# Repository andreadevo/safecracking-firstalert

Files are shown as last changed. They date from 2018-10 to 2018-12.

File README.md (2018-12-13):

# safecracking-firstalert
Building and designing a robot to open a safe with an unknown combination.

Link to photo and video documenation: http://bit.ly/first-alert-documentation

Try times:
100 possible numbers for 3 disks:
100x100x100 = 1,000,000 combinations
Each number can be +/- 1
Not likely or possible to duplicate numbers between disks
33x32x32 = 34,848
13 seconds per test means 5.25 days (without set testing)

We know the disks were only moved around and the first and last disk cannot move.
This means that the first number of the combination has to be 97 and the last must be 0.
1x33x32 = 1,056 combinations
13 seconds per test means 3.81 hours (without set testing)

After looking at the disks inside the safe we saw that they were split into 17 equal, numbered sections where interference points were placed.
The disk closest to the door had one interference point at 9 facing inward towards the safe.
The second two disks were identical and had interference points at 7 on one side and 3 on the other.
Then the disk farthest from the door had an interference point at 10 facing outward towards the door.
We know that the two middle disks are identical and only have two orientations.
We also know that the first and last disks cannot move or be changed.
So we have four possible orientations of the disks and their interference points.
(9)(7/3)(7/3)(10),
(9)(7/3)(3/7)(10),
(9)(3/7)(7/3)(10),
(9)(3/7)(3/7)(10).

This means there are only four possible combinations, one of which is the old one, so in reality, three possible combinations.
(97,32,44,0),
(97,32,??,0),
(97,??,44,0),
(97,??,??,0).

We can guess that most likely both middle disks were flipped to create more mystery
If we find which orientation the old disks were we can model the new orientation and find a range where the missing numbers could be so that we can make our blunt force test WAY faster than 4 hours. Ideally we should find a range of 10 or 15 which would be 3 to 5 set tests.
1x3x3 = 2 minutes
1x5x5 = 5.5 minutes

Even if we settled for finding a range of 48 values (figuring out right/left numbers of dial or top/bottom numbers of dial) it would be 16 tests.
1x16x16 = 55 minutes

Even though we ended up testing only 4 possible combinations, the blunt force test time for the right one (97, 7, 67) would be
1x2x50 = 25 minutes (testing up until getting the correct second number) + 1x1x34 = 8.5 minutes (last test with correct second number until reaching the correct 3rd number).
Being a total of 33.5 minutes to find this particular combination with our tests checking every other number to make up for any slop in the system.

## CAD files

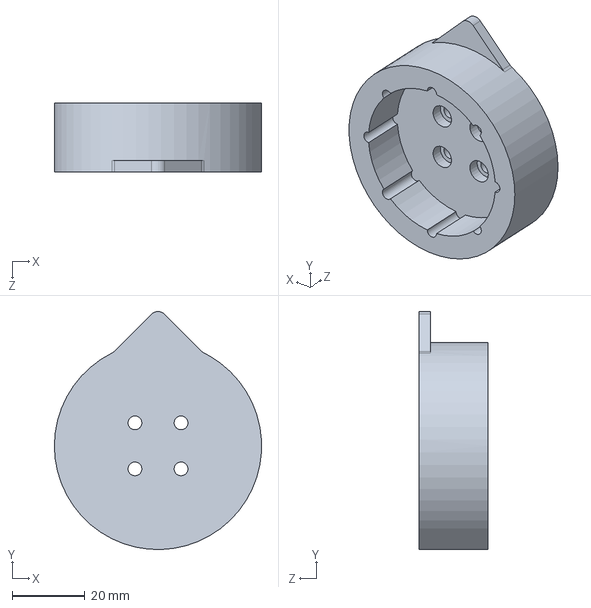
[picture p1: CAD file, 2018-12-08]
Parts/DIALCOUPLER.SLDPRT
57.1 x 65.6 x 19.1 mm

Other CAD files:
Parts/DIALCOUPLER.STL

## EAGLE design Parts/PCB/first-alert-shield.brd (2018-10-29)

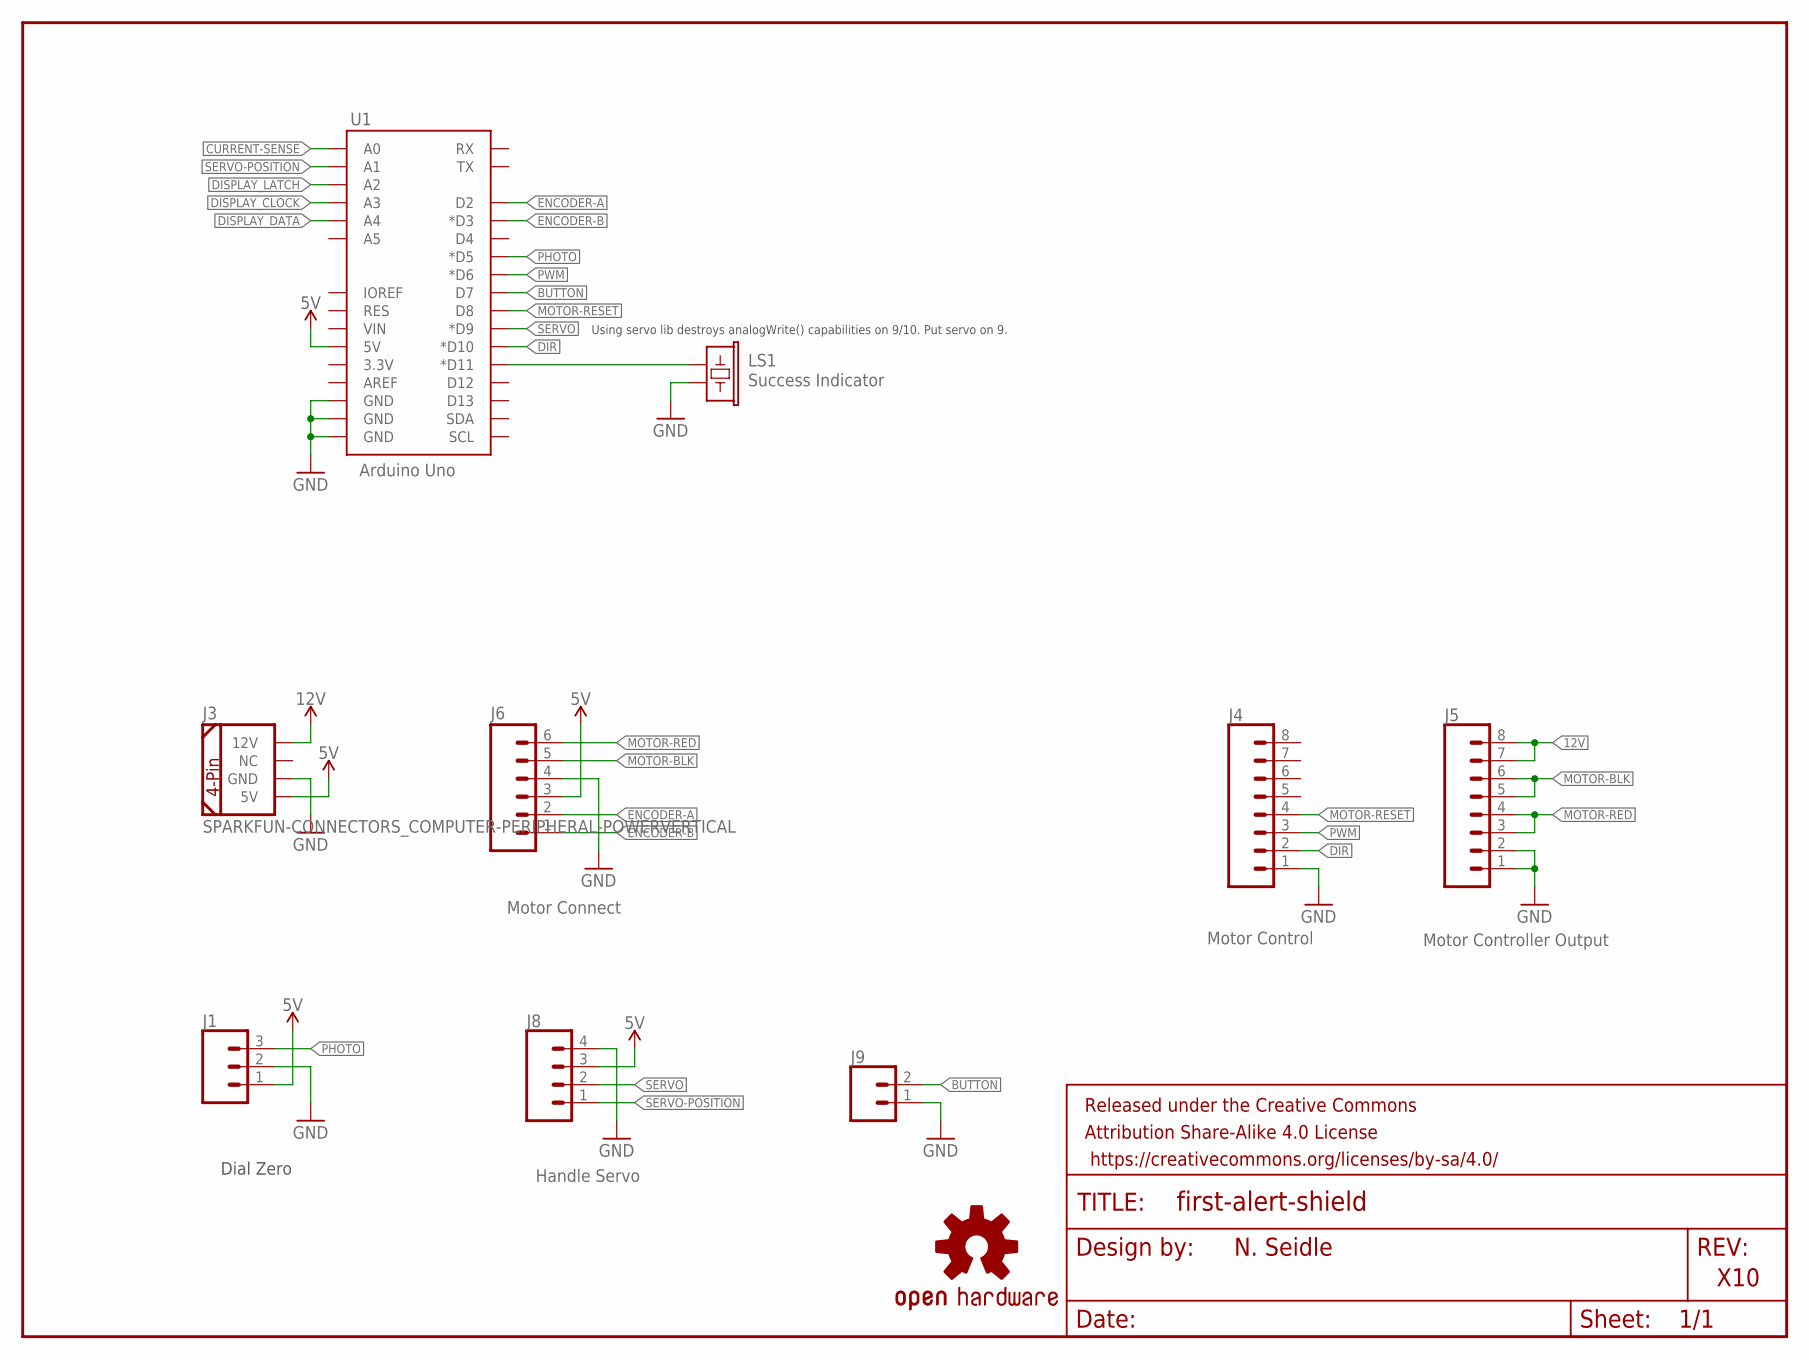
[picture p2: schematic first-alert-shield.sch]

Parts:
FRAME1: FRAME-LETTER; CREATIVE_COMMONS
J1: CONN_03JST-PTH-VERT; JST-3-PTH-VERT
J3: SPARKFUN-CONNECTORS_COMPUTER-PERIPHERAL-POWERVERT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; SPARKFUN-CONNECTORS_COMPUTER-PERIPHERAL-POWER
J4: Motor Control; 1X08
J5: Motor Controller Output; 1X08
J6: Motor Connect; 1X06@1
J8: Handle Servo; 1X04
J9: CONN_02JST-PTH-VERT; JST-2-PTH-VERT
LOGO2: OSHW-LOGOS; OSHW-LOGO-S
LS1: Success Indicator; BUZZER-12MM
U1: Arduino Uno; UNO_R3_SHIELD_NOLABELS

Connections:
5V: J1.1, J3.5V, J6.3, J8.3, U1.5V
12V: J3.12V, J5.7, J5.8
BUTTON: J9.2, U1.D7
BUZZ: LS1.+ (1), U1.D11 (*D11)
CURRENT-SENSE: U1.A0
DIR: J4.2, U1.D10 (*D10)
DISPLAY_CLOCK: U1.A3
DISPLAY_DATA: U1.A4
DISPLAY_LATCH: U1.A2
ENCODER-A: J6.2, U1.D2
ENCODER-B: J6.1, U1.D3 (*D3)
GND: J1.2, J3.GND, J4.1, J5.1, J5.2, J6.4, J8.4, J9.1, LS1.- (2), U1.GND@0 (GND), U1.GND@1 (GND), U1.GND@2 (GND)
MOTOR-BLK: J5.5, J5.6, J6.5
MOTOR-RED: J5.3, J5.4, J6.6
MOTOR-RESET: J4.4, U1.D8
PHOTO: J1.3, U1.D5 (*D5)
PWM: J4.3, U1.D6 (*D6)
SERVO: J8.2, U1.D9 (*D9)
SERVO-POSITION: J8.1, U1.A1

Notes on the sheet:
N. Seidle
X10
Using servo lib destroys analogWrite() capabilities on 9/10. Put servo on 9.
Dial Zero

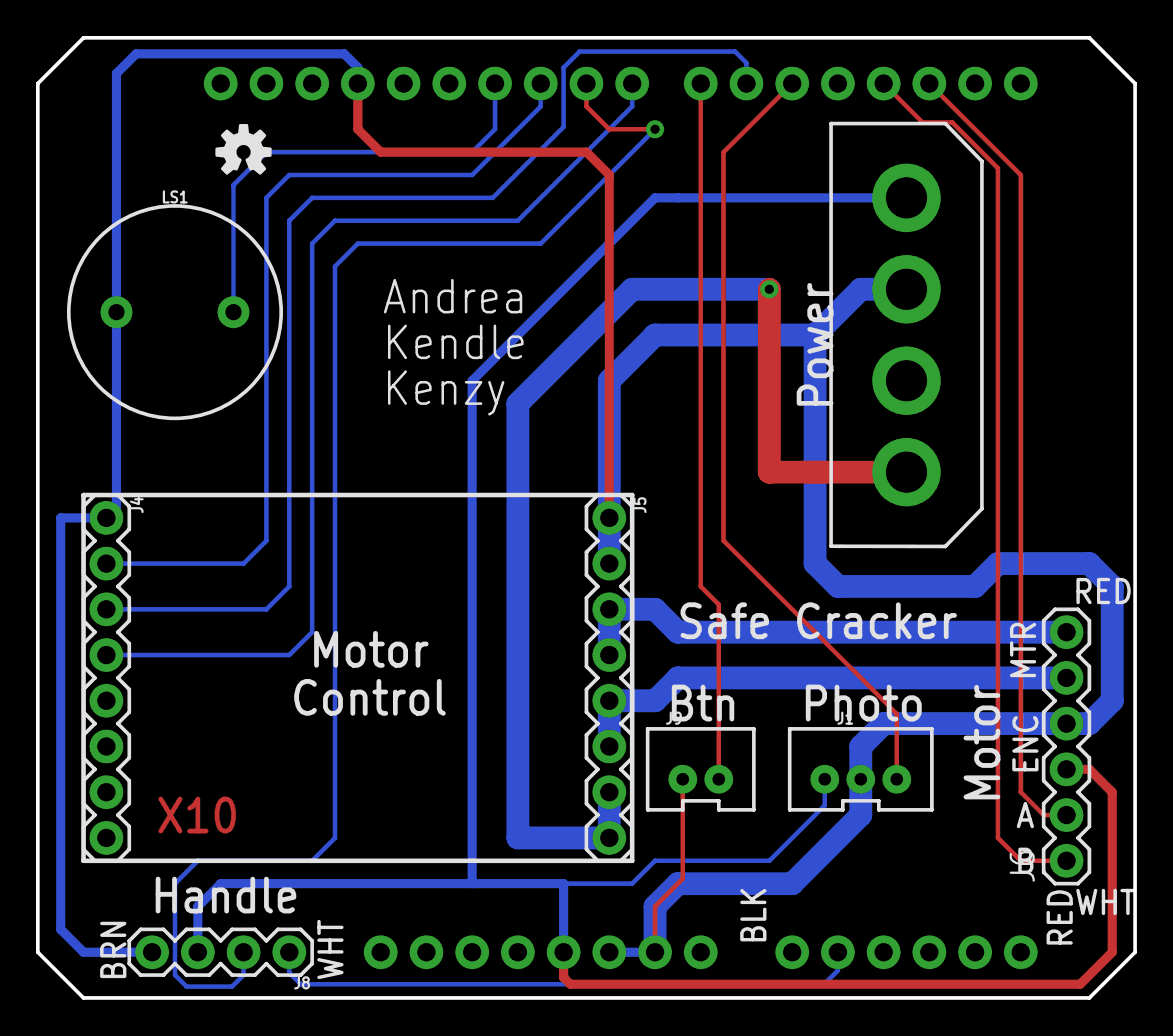
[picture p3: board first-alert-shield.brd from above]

Board: 2 copper layers, 61.0 x 53.3 mm, 11 parts (0 on the bottom side), 15 nets.

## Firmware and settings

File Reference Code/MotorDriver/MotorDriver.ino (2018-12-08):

/*
   Andrea DeVore
   Kenzy O'Neil
   Kendle
   Safecracking Class Fall 2018
   License: Open Source
*/

const int encoder0PinA = 2;
const int encoder0PinB = 3;
volatile unsigned int encoder0Pos = 0;

const int dirPin = 5;         // outputs the direction to dir pin on motor controller
const int pwmPin = 6;         // outputs high/low to PWM pin on motor controller, controls if motor is on/off
const int switchPin = 4;      // input from the switch, on/pff
const int photoGatePin = 7;   // input pin from photogate

int switchState;              // current state of the switch
int photoState;               // current state of the photogate

bool stateAChange = false;    // check if change has happened on A
bool stateBChange = false;    // check if change has happened on B

void setup() {
  // SETUP FOR ENCODER
  pinMode(encoder0PinA, INPUT_PULLUP);
  pinMode(encoder0PinB, INPUT_PULLUP);

  // encoder pin on interrupt 0 (pin 2)
  attachInterrupt(0, doEncoderA, CHANGE);
  // encoder pin on interrupt 1 (pin 3)
  attachInterrupt(1, doEncoderB, CHANGE);

  // SETUP FOR CONTROLS
  pinMode(dirPin, OUTPUT);
  pinMode(pwmPin, OUTPUT);
  pinMode(switchPin, INPUT);

  //LAUNCH MENU
  Serial.println("d)Dial position");
  Serial.println("h)Go home");

  Serial.begin(9600);
}

void loop() {
  //USER INPUT
  byte incoming;
  if (Serial.available()) {
    incoming = Serial.read();
    Serial.print("You pressed: ");
    Serial.write(incoming);
    Serial.println();

    // ROTATE DIAL TO USER INPUT
    if (incoming == 'd') {
      Serial.print("Enter dial position: ");
      while (!Serial.available());
      int dialPosition = Serial.parseInt();

      Serial.print("You told me to go to ");
      Serial.println(dialPosition);
      rotateDial(dialPosition);
    }
  }

  // LOOKS AT PHOTOGATE
  photoState = digitalRead(photoGatePin);
  if (photoState == HIGH) {
    // unbroken, motor on
    digitalWrite(pwmPin, HIGH);
  }
  else {
    // broken, motor off
    digitalWrite(pwmPin, LOW);
  }

  // LOOKS AT SWITCH
  switchState = digitalRead(switchPin);
  if (switchState == HIGH) {
    // switch on, CW
    digitalWrite(dirPin, HIGH);
  }
  else {
    // switch off, CCW
    digitalWrite(dirPin, LOW);
  }

  // CHECK IF ENCODER HAS MOVED
  if (stateAChange) {
    Serial.print ("A ");
    Serial.println (encoder0Pos, DEC);
    stateAChange = false;
  }
  if (stateBChange) {
    Serial.print ("B ");
    Serial.println (encoder0Pos, DEC);
    stateBChange = false;
  }
}

// ENCODER CODE
// encoder code from: playground.arduino.cc/Main/RotaryEncoders
void doEncoderA() {
  stateAChange = true;
  // look for a low-to-high on channel A
  if (digitalRead(encoder0PinA) == HIGH) {

    // check channel B to see which way encoder is turning
    if (digitalRead(encoder0PinB) == LOW) {
      encoder0Pos = encoder0Pos + 1;         // CW
    }
    else {
      encoder0Pos = encoder0Pos - 1;         // CCW
    }
  }
  // must be a high-to-low edge on channel A
  else   {
    // check channel B to see which way encoder is turning
    if (digitalRead(encoder0PinB) == HIGH) {
      encoder0Pos = encoder0Pos + 1;          // CW
    }
    else {
      encoder0Pos = encoder0Pos - 1;          // CCW
    }
  }
}

void doEncoderB() {
  stateBChange = true;
  // look for a low-to-high on channel B
  if (digitalRead(encoder0PinB) == HIGH) {

    // check channel A to see which way encoder is turning
    if (digitalRead(encoder0PinA) == HIGH) {
      encoder0Pos = encoder0Pos + 1;         // CW
    }
    else {
      encoder0Pos = encoder0Pos - 1;         // CCW
    }
  }

  // Look for a high-to-low on channel B

  else {
    // check channel B to see which way encoder is turning
    if (digitalRead(encoder0PinA) == LOW) {
      encoder0Pos = encoder0Pos + 1;          // CW
    }
    else {
      encoder0Pos = encoder0Pos - 1;          // CCW
    }
  }
}
//
//int convertToSteps(){
//
//}

void launchMenu() {
  Serial.println("d)Dial position");
  Serial.println("h)Go home");
}

void rotateDial(int rotate){
  while (encoder0Pos < 8600){
    digitalWrite(pwmPin, HIGH);   //turns motor on
  }
  digitalWrite(pwmPin, HIGH);
}
//void rotateCCW(int numSteps){
//
//}
//
//void setDialSpeed(int rotationSpeed){
//
//}
//
//void detectFlag(){
//
//}
//
//void goHome(){
//
//}

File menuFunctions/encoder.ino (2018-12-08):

//playground.arduino.cc/Main/Rotary/Encoders

////////////////////////////////
// CHECK IF ENCODER HAS MOVED //
////////////////////////////////

void encoderState() {
  if (stateAChange) {
    Serial.print ("A ");
    Serial.println (encoder0Pos, DEC);
    stateAChange = false;
  }
  if (stateBChange) {
    Serial.print ("B ");
    Serial.println (encoder0Pos, DEC);
    stateBChange = false;
  }
}

////////////////////
// ENCODER A CODE //
////////////////////

void doEncoderA() {
  // look for a low-to-high on channel A
  stateAChange = true;
  if (currentDirection == CCW) {
    encoder0Pos++;
  } else {
    encoder0Pos--;
  }

  // Reset counter
  if (encoder0Pos > totalTicks) {
    encoder0Pos = 0;
  }
  else if (encoder0Pos < 0) {
    encoder0Pos = totalTicks;
  }
}

////////////////////
// ENCODER B CODE //
////////////////////

void doEncoderB() {
  // look for a low-to-high on channel B
  stateBChange = true;
  if (currentDirection == CCW) {
    encoder0Pos++;
  } else {
    encoder0Pos--;
  }
  // Reset counter
  if (encoder0Pos > totalTicks) {
    encoder0Pos = 0;
  }
  else if (encoder0Pos < 0) {
    encoder0Pos = totalTicks;
  }
}

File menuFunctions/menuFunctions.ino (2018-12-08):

/*
   Andrea DeVore
   Kenzy O'Neil
   Kendle McDowell
   Safecracking Class Fall 2018
   License: Open Source
*/

//Key for PCB Pins//////////
//  dirPin = D10          //
//  pwmPin = D6           //
//  motorReset = D8       //
//  photoPin = D5         //
//  redButton = D7        //
//  whiteButton = A1      //
//  servoPin = D9         //
//  buzzerPin = D11       //
////////////////////////////

#include "nvm.h" //EEPROM locations for settings
#include <EEPROM.h> //For storing settings and things to NVM

const int encoder0PinA = 2;
const int encoder0PinB = 3;
volatile int encoder0Pos = 0;

const int dirPin = 10;        // outputs the direction to dir pin on motor controller
const int pwmPin = 6;         // outputs high/low to PWM pin on motor controller, controls if motor is on/off
const int switchPin = 4;      // input from the switch, on/pff
const int photoGatePin = 5;   // input pin from photogate
const int buzzerPin = 11;

int switchState;              // current state of the switch
int photoState;               // current state of the photogate

bool stateAChange = false;    // check if change has happened on A
bool stateBChange = false;    // check if change has happened on B

int flagPos;                  // tracks home positon of motor;
int cwOffset;                 // clockwise offset from 0
int ccwOffset;                // counterclockwise offset from 0
int posZero;                  // zero on dial
int goToHome;                 // saving home
int motorSpeed = 200;         // speed from 0-255, written to pwmPin
const int ticks = 85;         // number of ticks per dial position
int totalTicks = (ticks * 99) - 1; //total number of ticks in a rotation
int offset = 20;
bool win = false;


boolean currentDirection = 0; // track the direction to encoder
const byte CW = 0;
const byte CCW = 1;


///////////
// SETUP //
///////////

void setup() {
  // encoder setup
  pinMode(encoder0PinA, INPUT_PULLUP);
  pinMode(encoder0PinB, INPUT_PULLUP);

  // encoder pin on interrupt 0 (pin 2)
  attachInterrupt(0, doEncoderA, CHANGE);
  // encoder pin on interrupt 1 (pin 3)
  attachInterrupt(1, doEncoderB, CHANGE);

  // SETUP FOR CONTROLS
  pinMode(dirPin, OUTPUT);
  pinMode(pwmPin, OUTPUT);
  pinMode(switchPin, INPUT);
  pinMode(buzzerPin, OUTPUT);

  Serial.begin(9600);
}



/////////////////////////
// LAUNCH MENU OPTIONS //
/////////////////////////

void loop() {
  int incoming;
  Serial.println("1)Home the Dial");
  Serial.println("2)Enter Dial Position");
  Serial.println("3)Test Saved Combo");
  Serial.println("4)Crack the Safe");
  Serial.println("5)Access EEPROM");
  Serial.println("6)CCW");
  Serial.println("7)CW");

  while (!Serial.available());            // do nothing, wait for user input

  incoming = Serial.parseInt();
  Serial.print("You pressed: ");
  Serial.println(incoming);

  ///////////////
  // MAIN MENU //
  ///////////////

  // ---------- HOME THE DIAL ----------
  if (incoming == 1) {
    // user inputs flag position, puts to EEPROM, maps the encoder to the dial
    findHome();
  }

  // ---------- ENTER THE DIAL POSITION ----------
  else if (incoming == 2) {
    // user inputs where to go
    rotateDial();
  }

  // ---------- TEST SAVED COMBO ----------
  else if (incoming == 3) {
    // uses code to open safe with a saved combo
    openSafe();
  }

  // ---------- CRACK THE SAFE ----------
  else if (incoming == 4) {
    // calls function to guess every combination until it finds the correct one
    while (win == false)
      crackTheSafe();
  }

  // ---------- ACCESS EEPROM ----------
  else if (incoming == 5) {
    // change EEPROM values
    int subIncoming;
    Serial.println("1)Change speed");
    Serial.println("2)Change combination");

    while (!Serial.available());            // do nothing, wait for user input
    subIncoming = Serial.parseInt();
    Serial.print("You pressed: ");
    Serial.println(subIncoming);

    if (subIncoming == 1) {
      Serial.println("Change speed");
    }
    else if (subIncoming == 2) {
      Serial.println("Change combination");
    }
    else {
      Serial.println("Not a valid menu option. Please try again.");
    }
  }

  // ---------- CCW ----------
  else if (incoming == 6) {
    setDir(CCW);
    analogWrite(pwmPin, motorSpeed);
    photoState = digitalRead(photoGatePin);
    analogWrite(pwmPin, motorSpeed);     // turns motor on
    while (photoState == HIGH) {
      photoState = digitalRead(photoGatePin);
    }
    digitalWrite(pwmPin, LOW);          // turns motor off
  }

  // ---------- CW ----------
  else if (incoming == 7) {
    setDir(CW);
    photoState = digitalRead(photoGatePin);
    analogWrite(pwmPin, motorSpeed);    // turns motor on
    while (photoState == HIGH) {
      Serial.println (encoder0Pos, DEC);
      photoState = digitalRead(photoGatePin);
    }
    digitalWrite(pwmPin, LOW);          // turns motor off
  }

  // ---------- DEFAULT: TRY AGAIN ----------
  else {
    Serial.println("Not a valid menu option. Please try again.");
  }
}

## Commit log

2018-09-26 handle puller model prototype with lever
    [handlepullerTrial6.SLDPRT]
2018-09-26 basic handle puller prototype
    [handle-puller.step]
2018-09-26 3D Print FIles Handle and Coupler
    [DIALCOUPLER.STL, HANDLEPULLER.STL]
2018-10-07 cleaning out repo to only have final products
    [handle-puller.step, handlepullerTrial6.SLDPRT]
2018-10-07 cleaning up github repo into final group documentation
    [DIALCOUPLER.STL, HANDLEPULLER.STL]
2018-10-08 Update MotorDriver/MotorDriver.ino
    Motor Driver code that changes motor direction and stops the motor with a photogate
2018-10-08 Update MotorDriver/MotorDriver.ino
    Changed encoder readings and print statements
2018-10-10 sketch to check encoder reset
    [motor-driver-user-input.ino]
2018-10-10 sketch to check resetting encoder
    [rotate-dial.ino]
2018-10-10 Encoder ticks working in both directions.
2018-10-10 Home changed and encoder ticks converted to dial positions.
2018-10-15 Cleaned up prints and created an error message for nonexistant dial positions.
    [motor-driver-user-input.ino]
2018-10-17 Changed menu and broke functions into tabs.
    [motor-driver-user-input.ino, rotateDial.ino]
2018-10-29 first attempt altering PCD board, removed extra components, altered power connector, reconnected traces from power connector
    [first-alert-shield.brd, first-alert-shield.sch]
2018-10-31 Motor rotates correctly to put in the combination,
    [controlFunctions.ino, encoder.ino, openSafe.ino]
2018-12-03 Encoder is fixed and we have a working sanity sketch
    [crackTheSafe.ino, encoder.ino, menuFunctions.ino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]
2018-12-05 Encoder "mostly" calibrated
2018-12-05 We're calibrated!
2018-12-05 Slow down functions implemented, still kind of fine tuning calibration
2018-12-08 3D models for safe
    [DIALCOUPLER.STL]
2018-12-08 Updated coupler
    [DIALCOUPLER.SLDPRT, DIALCOUPLER.STL]
2018-12-10 Changed a few numbers added a few prints

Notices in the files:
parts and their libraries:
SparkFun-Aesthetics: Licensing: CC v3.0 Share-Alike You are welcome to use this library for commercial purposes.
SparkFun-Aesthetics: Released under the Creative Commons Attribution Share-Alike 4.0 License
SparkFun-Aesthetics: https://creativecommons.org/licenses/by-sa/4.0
